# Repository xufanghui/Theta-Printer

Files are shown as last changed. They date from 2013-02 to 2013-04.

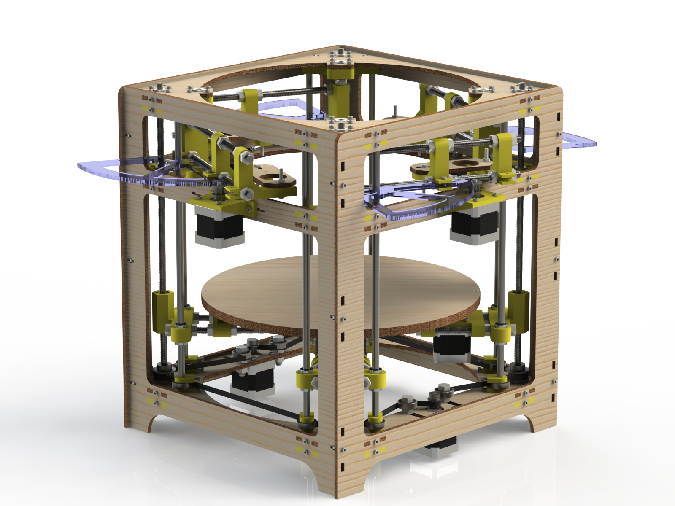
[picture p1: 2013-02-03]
Renders/theta_printer_12.png

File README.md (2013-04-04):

Theta Printer
=============

A polar coordinate based 3D printer with 4 extruders

A magnificent rendering of the Quadricator
[Full Size](http://i.imgur.com/XjrklZc.jpg)

Whats a polar printer?
----------------------
A polar printer works kind of like an old fashioned record player. Your objects are printed onto a platter which spins. The advantage is that you can have many print heads. Each extruder is on the end of an arm which swings in and out. The spinning platter is called the ϴ ("theta") axis and the swinging arm is called the R axis. Together these replace the normal X and Y coordinates you're used to.

Features
--------
+ 4 extruders for multiple colors and materials
+ 320 mm build platter
+ 80425 mm^2 print area (bigger than most repraps)
+ 0.084 degrees/step angular resolution (ϴ Axis)
+ 0.20 mm/step linear resolution (R Axis)
+ Now comes in two versions! The lasercut edition and the reprap edition (printed parts & threaded rods)

ϴ Axis
------
A wooden disk, under which resides a complicated set of motors gears rods and bearings
[Full Size](http://i.imgur.com/GR4uxWu.png)

Objects are printed onto a platter that spins back and forth. Its driven via a stepper motor and a large gear. Rollers support the platter around the perimeter and keep it level.

R Axis
------
Four robotic arms arranged in a diamond shape
[Full Size](http://i.imgur.com/bllIclA.png)

Four Extruders are each mounted on the end of an arm that swings in and out. The blue protractor things are gears for moving the arms.

Z Axis
------
A set of four sprockets with the associated pulleys, motors, and drive belt
[Full Size](http://i.imgur.com/wnbYKVQ.png)

The Z axis is nothing new. Threaded rods in each corner are synchronized by a timing belt and driven by two stepper motors.

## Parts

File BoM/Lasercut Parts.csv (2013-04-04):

ITEM NO. | PART NUMBER | DESCRIPTION | QTY.
1 | Head Holder |  | 8
2 | Arm Rod |  | 8
3 | M8.Nut |  | 149
4 | Arm Center |  | 4
5 | Arm Axis Rod |  | 4
6 | R Gear |  | 4
7 | M3x16.Bolt.91290A120 |  | 172
8 | Extruder Mount Plate |  | 4
9 | M4x30.Bolt.91280A148 |  | 8
10 | M4.Nut.90591A141 |  | 8
11 | Level 1 Corner |  | 8
12 | 608RS Bearing |  | 36
13 | 608 Bearing Cap |  | 1
14 | M3.Nut.90591A121 |  | 172
15 | R Motor Mount |  | 4
16 | Base |  | 7
17 | Cuerpo |  | 7
18 | Tapa |  | 7
19 | B18.6.7M - M3 x 0.5 x 5 Type I Cross Recessed PHMS --5N |  | 28
20 | Eje |  | 7
21 | AFBMA 12.1.4.1 - 0050-11 - 10 | SI | NC | 10_68 | 14
22 | M3x10.Bolt.91290A115 |  | 28
23 | Motor.Sprocket |  | 7
24 | Theta Center |  | 1
25 | M3x30.Bolt.91290A130 |  | 4
26 | Level Z Corner |  | 4
27 | Linear Bearing Body |  | 8
28 | Linear Bearing inside |  | 8
29 | Platter Rod |  | 4
30 | Theta Motor Mount |  | 1
31 | Platter Top |  | 1
32 | Platter Bottom |  | 1
33 | M3x16.Countersunk.Bolt.91294A134 |  | 4
34 | Platter Axle |  | 1
35 | M8.Washer.91455A130 |  | 8
36 | Theta Gear |  | 1
37 | Platter Roller Mount High |  | 1
38 | M8x20.Bolt.91310A533 |  | 3
39 | Platter Roller Mount Low |  | 2
40 | Level 4 Corner |  | 4
41 | Z Smooth Rod |  | 8
42 | Z Rod |  | 4
43 | Z.Rod.Sprocket.a_6z51-036df0610 |  | 4
44 | Smooth Rod Clamp |  | 16
45 | Belt1-1 |  | 1
46 | Level 1 Side |  | 1
47 | Level 2 Side |  | 1
48 | Level 4 Side |  | 1
49 | M8x30.Bolt.91310A536 |  | 4
50 | Side 1 |  | 2
51 | Side 2 |  | 2
52 | 91166A210 |  | 8

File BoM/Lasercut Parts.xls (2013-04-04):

Acquired? | Printed Parts | Description | Qty
1 | Head Holder |  | 8
 | Level 1 Corner |  | 8
✓ | Motor Sprocket |  | 7
✓ | Arm Center |  | 4
 | Level 4 Corner |  | 4
 | Level Z Corner |  | 4
✓ | R Motor Mount |  | 4
✓ | Z Rod Sprocket |  | 4
✓ | Platter Roller Middle |  | 3
 | Theta Center |  | 1
 | Theta Motor Mount |  | 1
 | Laser Cut Parts | Description | Qty | Cost
3 | R Gear | 5mm Acrylic | 4
✓ | Theta Gear | 5mm Acrylic | 1
✓ | Extruder Mount Plate | 5mm Plywood | 4
✓ | Platter Top | 5mm Plywood | 1
✓ | Platter Bottom | 5mm Plywood | 1
✓ | Level 1 Side | 5mm Plywood | 1
✓ | Level 2 Side | 5mm Plywood | 1
✓ | Level 4 Side | 5mm Plywood | 1
✓ | Side 1 | 5mm Plywood | 2
✓ | Side 2 | 5mm Plywood | 2
✓ | 608 Bearing Cap | 5mm Plywood | 1
✓ | Platter Roller Side High |  | 4
✓ | Platter Roller Side Low |  | 2
 | Total |  |  | $60
 | Threaded Rods | Description | Qty | Length (mm) | Total Length | Purchase Qty | Price/Meter | Subtotal
✓ | Arm Rod | M8 1.25 Pitch | 8 | 220 | 1760 | 2000
✓ | Arm Axis Rod | M8 1.25 Pitch | 4 | 110 | 440 | 1000
✓ | Platter Rod | M8 1.25 Pitch | 4 | 400 | 1600 | 2000
✓ | Platter Axle | M8 1.25 Pitch | 1 | 55 | 55 | 1000
✓ | Z Rod | M8 1.25 Pitch | 4 | 430 | 1720 | 2000
✓ | Total |  |  |  | 5575 | 8000 | 4.29 | $34.32 | McMaster | 99055A125 | http://www.mcmaster.com/#catalog/119/3147/=liic32
 | Smooth Rod
✓ | Z Smooth Rod | M8 | 8 | 350 | 2800 | 3200 |  | $49.56 | AliExpress | 707204369 | http://www.aliexpress.com/item/CNC-2pcs-Linear-shaft-400mm-long-diameter-8mm-L-400mm-harden-linear-rod-round-shaft-chrome/707204369.html
 |  |  |  |  |  | 12ft |  | $27.28 | McMaster | 89095K15 | http://www.mcmaster.com/#89095K15
 | Vitamins | Description | Qty | Purchase Qty | Price Each | Subtotal | Supplier | Part # | Link
✓ | 608ZZ Bearing |  | 28 |  |  |  | AliExpress | 609983490 | http://www.aliexpress.com/item/50pcs-lot-608ZZ-608-2RS-8-22-7-Deep-groove-ball-bearing-skate-wheel-bearing/609983490.html
✓ | LM8UU Linear Bearing |  | 8 |  |  |  | AliExpress | 488396282 | http://www.aliexpress.com/item/LM8UU-8mm-Linear-Ball-Bearing-Bush-Bushing-New/488396282.html
✓ | M3.Nut.90591A121 |  | 172 | 200 |  | 2.78 | McMaster | 90591A121 | http://www.mcmaster.com/#catalog/119/3167/=l4j9dm
✓ | M3x10.Bolt.91290A115 |  | 28 | 100 |  | 5.02 | McMaster | 91290A115 | http://www.mcmaster.com/#catalog/119/3093/=l4j9n6
✓ | M3x16.Bolt.91290A120 |  | 176 | 200 |  | 12.1 | McMaster | 91290A120 | http://www.mcmaster.com/#catalog/119/3093/=l4j9rl
✓ | M3x16.Countersunk.Bolt.91294A134 |  | 4 | 100 |  | 11.67 | McMaster | 91294A134 | http://www.mcmaster.com/#catalog/119/3102/=l4ja5r
✓ | M3x30.Bolt.91290A130 |  | 4 | 0 |  | 0 | McMaster | 91290A130 | http://www.mcmaster.com/#catalog/119/3093/=l4jb78
✓ | M4.Nut.90591A141 |  | 8 | 100 |  | 1.39 | McMaster | 90591A141 | http://www.mcmaster.com/#catalog/119/3167/=l4jbpz
✓ | M4x30.Bolt.91280A148 |  | 8 | 100 |  | 7.96 | McMaster | 91280A148 | http://www.mcmaster.com/#catalog/119/3129/=l4jcc0
✓ | M8.Nut | 1.25mm Pitch | 149 | 200 |  | 9.02 | McMaster | 90592A022 | http://www.mcmaster.com/#hex-nuts/=l4je22
✓ | M8.Washer.91455A130 |  | 8 | 100 |  | 6.09 | McMaster | 91455A130 | http://www.mcmaster.com/#catalog/119/3202/=l4jej3
✓ | M8x20.Bolt.91310A533 |  | 3 | 0 |  | 0 | McMaster | 91310A533 | http://www.mcmaster.com/#catalog/119/3128/=l4jf1j
✓ | M8x30.Bolt.91310A536 |  | 4 | 25 |  | 7.91 | McMaster | 91310A536 | http://www.mcmaster.com/#standard-cap-screws/=ld4026
 | Motor.Sprocket | 18 Grooves | 7 | 0 | 5.81 | 0 | SDP/SI | A 6T16M018DF6005 | https://sdp-si.com/eStore/PartDetail.asp?Opener=Group&PartID=42977&GroupID=347
4 | NEMA 17 |  | 7
✓ | Z Belt | GT2 1210.00 mm | 1 | 1 | 9.32 | 9.32 | SDP/SI | A 6R51M605060 | https://sdp-si.com/eStore/PartDetail.asp?Opener=Order&PartID=75945&GroupID=342&Qty=0
✓ | Z Belt | GT2 1228.00 mm | 1 | 1 | 9.32 | 9.32 | SDP/SI | A 6R51M614060 | https://sdp-si.com/eStore/PartDetail.asp?Opener=Order&PartID=75946&GroupID=342&Qty=0
 | Z.Rod.Sprocket |  | 4 | 0 | 6.18 | 0 | SDP/SI | A 6Z51-036DF0610 | https://sdp-si.com/eStore/PartDetail.asp?Opener=Group&PartID=55833&GroupID=218
 | Total |  |  |  |  | $82.58
 | Total Cost | $226.46

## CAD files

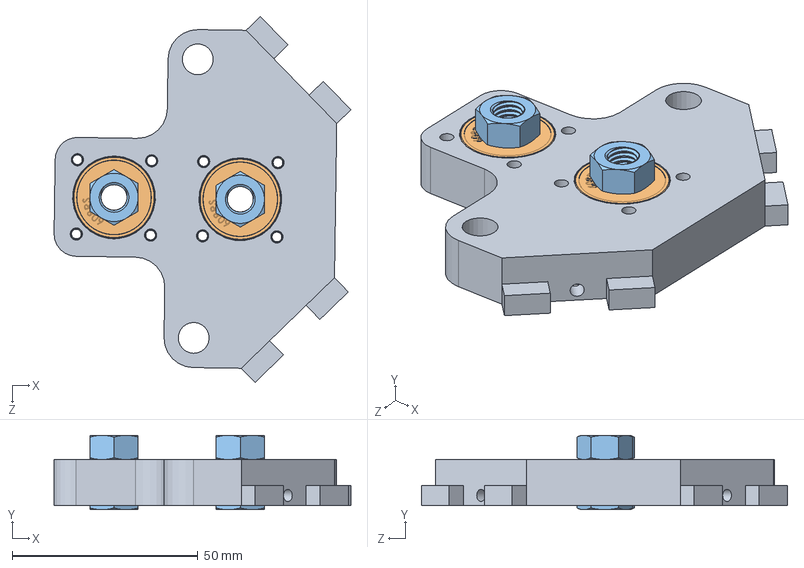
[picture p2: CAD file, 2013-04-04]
Level 1 Corner Assembly.SLDASM
79.9 x 20.0 x 98.5 mm
Level 1 Corner
608RS Bearing x 2
M8.Nut x 4
M3.Nut.90591A121 x 8

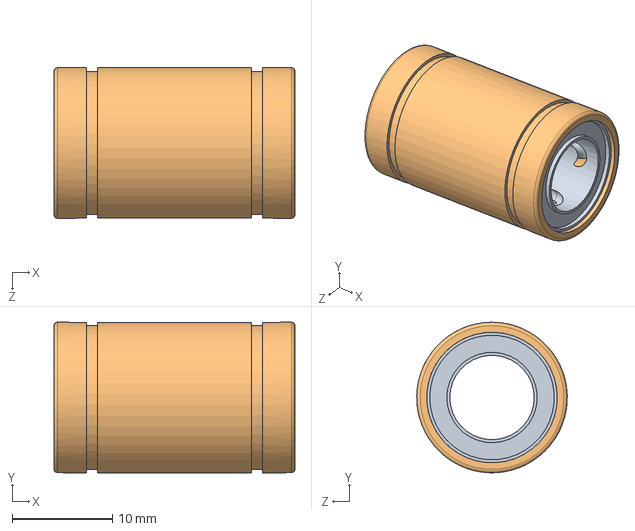
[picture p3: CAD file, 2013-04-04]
Vitamins/LM8UU/Linear Bearing animation.SLDASM
24.0 x 15.0 x 15.0 mm
Linear Bearing Body
Linear Bearing inside

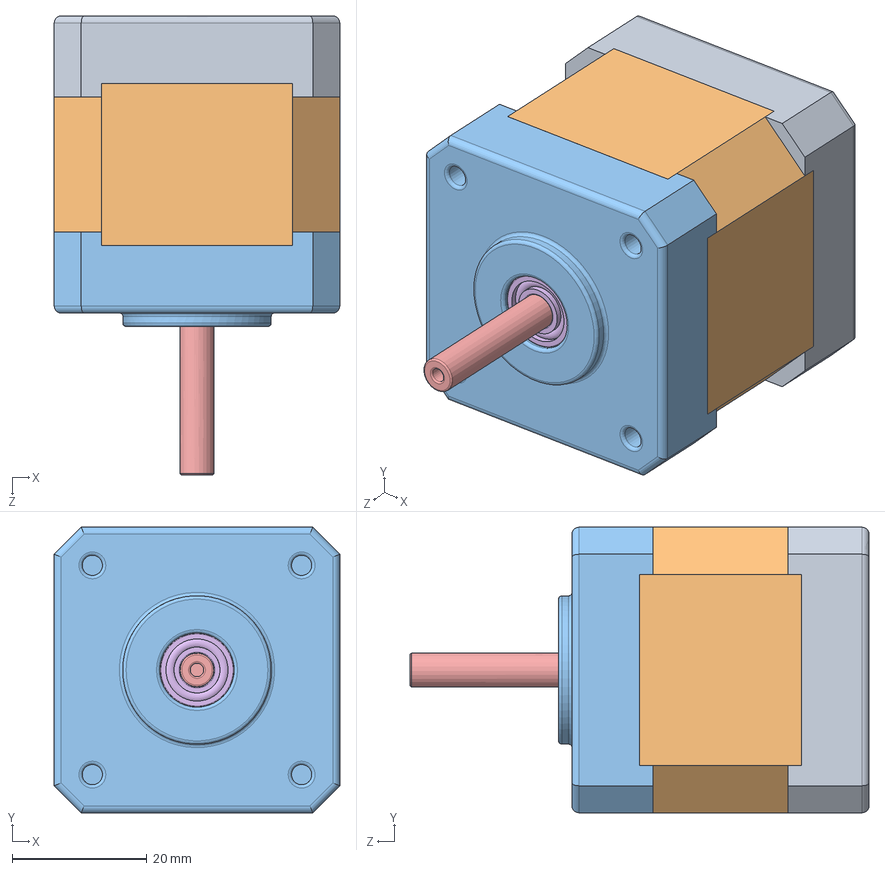
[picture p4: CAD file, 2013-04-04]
Vitamins/NEMA 17/NEMA 17.SLDASM
42.3 x 42.3 x 68.0 mm
Base
Cuerpo
Tapa
pan cross head_am x 4
Eje
instrument ball bearing_68_am x 2

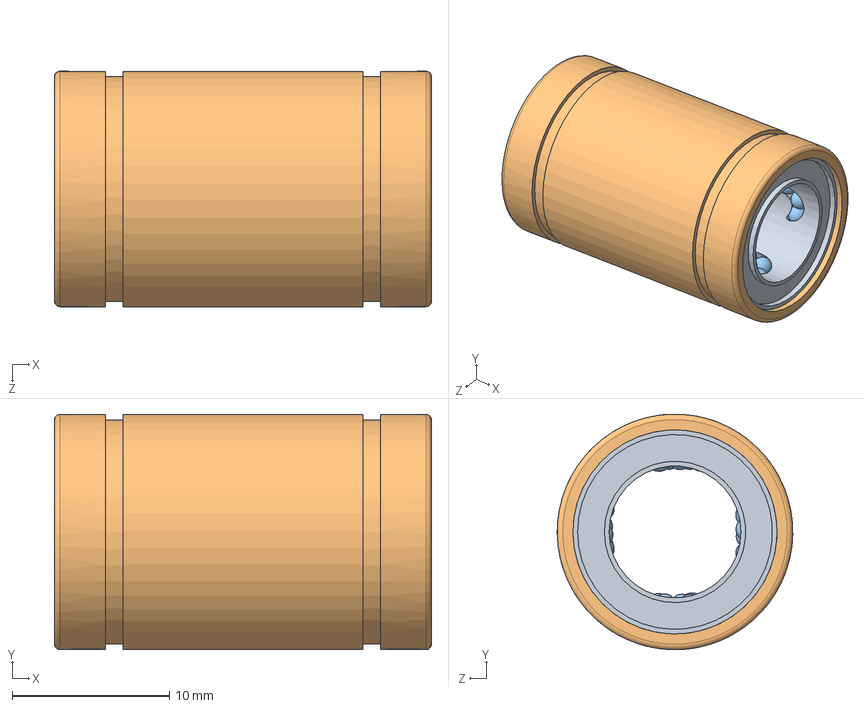
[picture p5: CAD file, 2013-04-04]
Vitamins/LM8UU/LU8MM.SLDASM
24.0 x 15.0 x 15.0 mm
Linear Bearing Body
Linear Bearing inside
Municion x 102

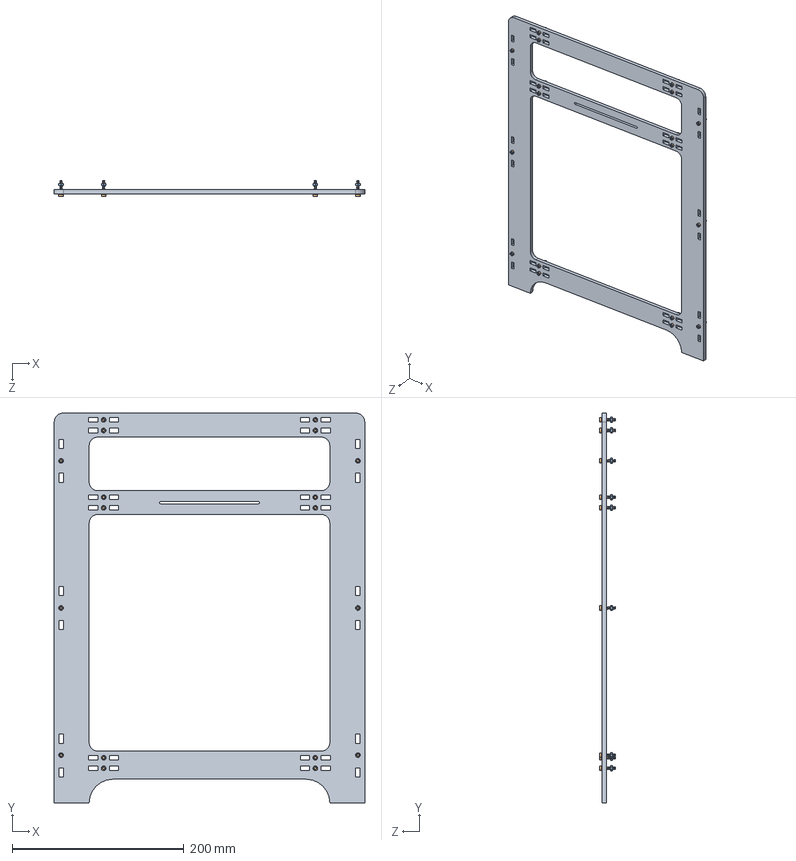
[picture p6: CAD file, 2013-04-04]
Side 2 Assembly.SLDASM
361.3 x 453.7 x 19.0 mm
Side 2
M3x16.Bolt.91290A120 x 18
M3.Nut.90591A121 x 18

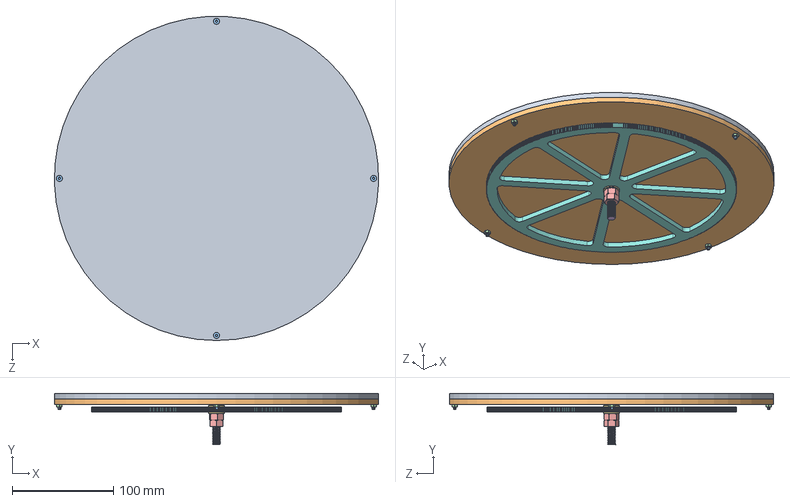
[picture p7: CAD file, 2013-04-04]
Platter Assembly.SLDASM
319.9 x 50.6 x 319.7 mm
Platter Top
Platter Bottom
M3x16.Countersunk.Bolt.91294A134 x 4
M3.Nut.90591A121 x 4
M8.Nut x 3
Platter Axle
M8.Washer.91455A130 x 2
Theta Gear

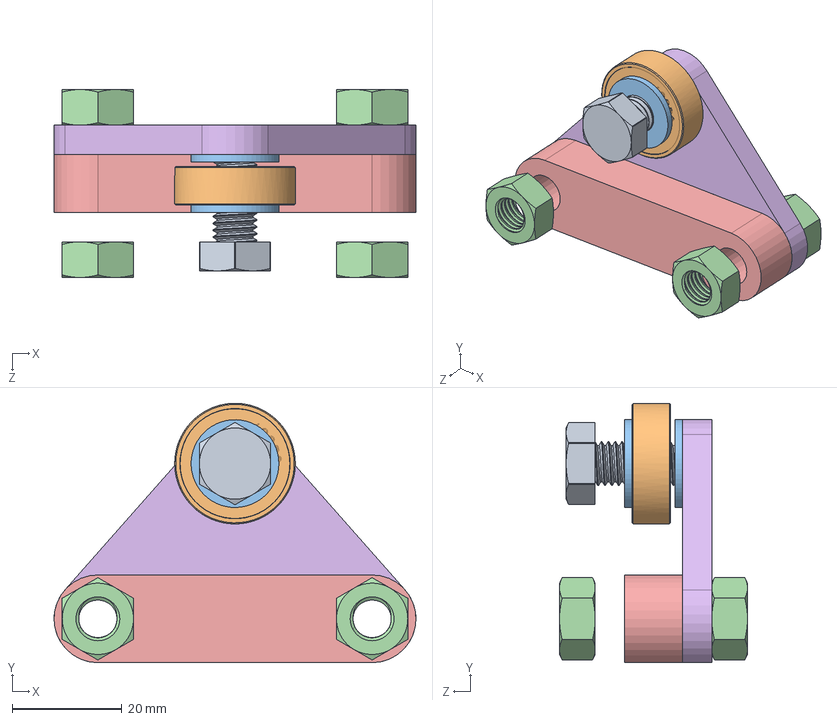
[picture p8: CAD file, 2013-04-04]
Platter Roller Assembly.SLDASM
66.0 x 47.3 x 34.3 mm
M8x20.Bolt.91310A533
608RS Bearing
M8.Washer.91455A130 x 2
M8.Nut x 4
Platter Roller Middle
Platter Roller Side

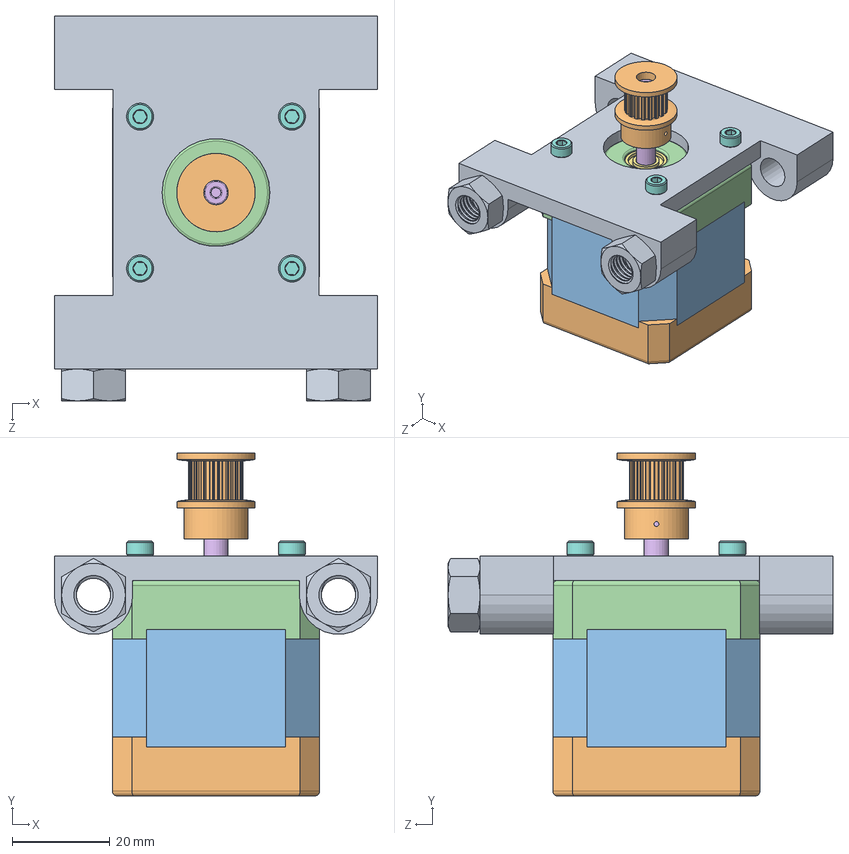
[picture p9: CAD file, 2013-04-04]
Theta Motor Assembly.SLDASM
66.0 x 70.0 x 78.5 mm
Theta Motor Mount
Base
Cuerpo
Tapa
pan cross head_am x 4
Eje
instrument ball bearing_68_am x 2
M3x10.Bolt.91290A115 x 4
M8.Nut x 2
Motor.Sprocket

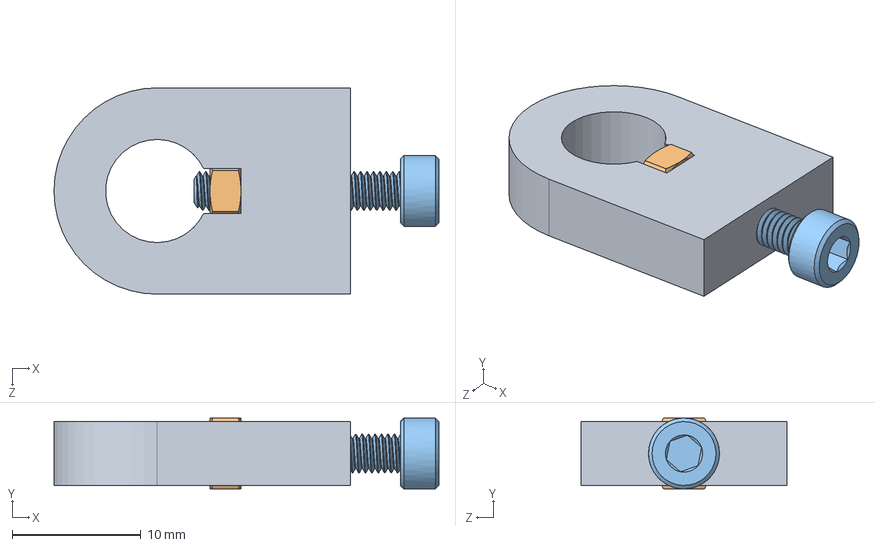
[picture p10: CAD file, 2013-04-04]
Smooth Rod Clamp Assembly.SLDASM
29.9 x 5.50 x 16.0 mm
Smooth Rod Clamp
M3.Nut.90591A121
M3x16.Bolt.91290A120

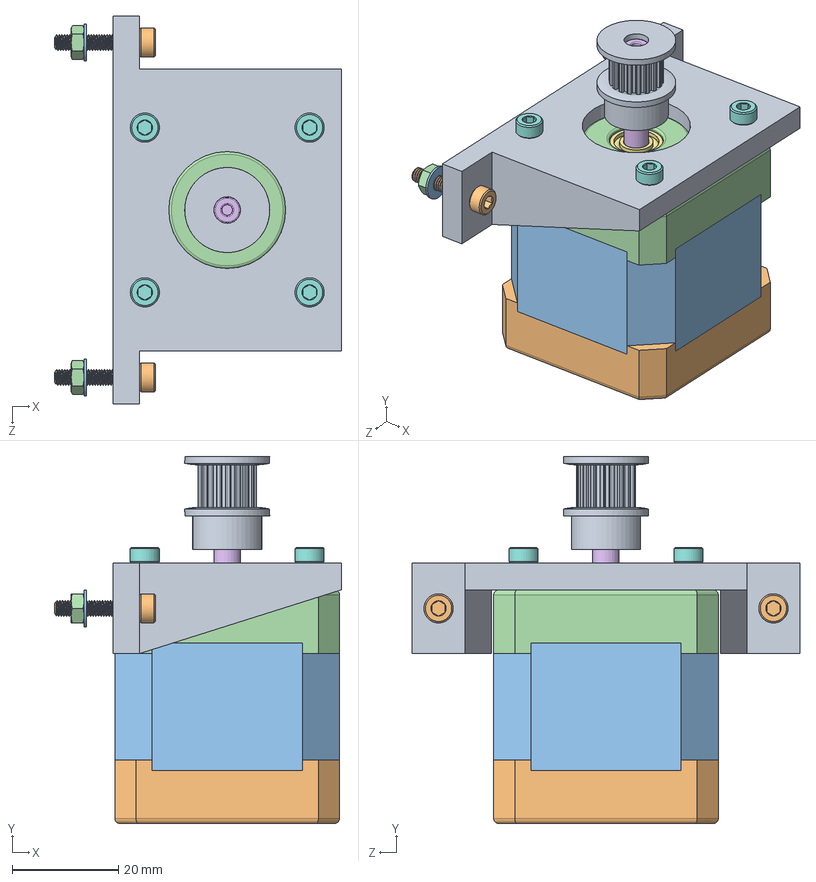
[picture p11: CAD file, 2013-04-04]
R Motor Assembly.SLDASM
54.0 x 69.1 x 73.0 mm
R Motor Mount
Base
Cuerpo
Tapa
pan cross head_am x 4
Eje
instrument ball bearing_68_am x 2
M3x10.Bolt.91290A115 x 4
Motor.Sprocket
M3x16.Bolt.91290A120 x 2
M3.Washer.91166A210 x 2
M3.Nut.90591A121 x 2

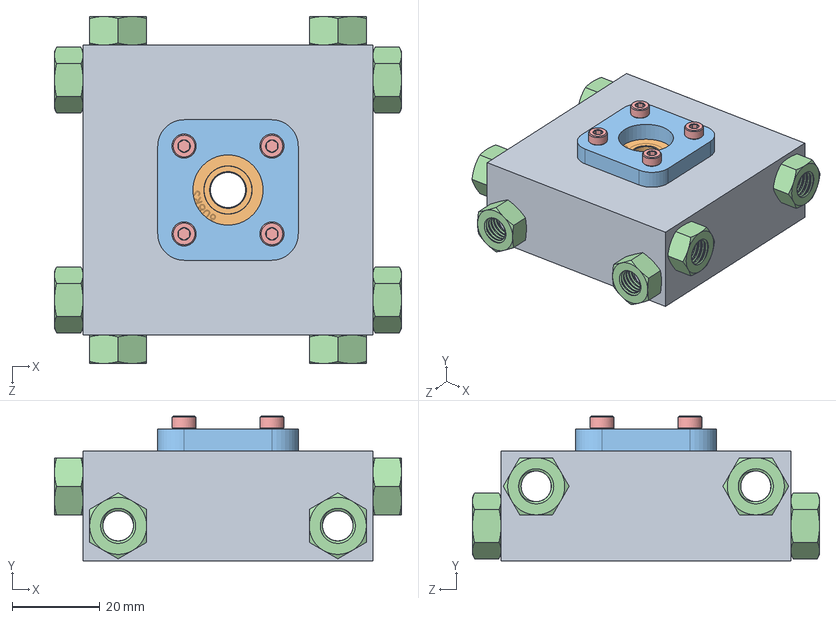
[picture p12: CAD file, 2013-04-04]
Theta Center Assembly.SLDASM
79.0 x 33.0 x 79.0 mm
Theta Center
608RS Bearing
608 Bearing Cap
M8.Nut x 8
M3x16.Bolt.91290A120 x 4
M3.Nut.90591A121 x 4

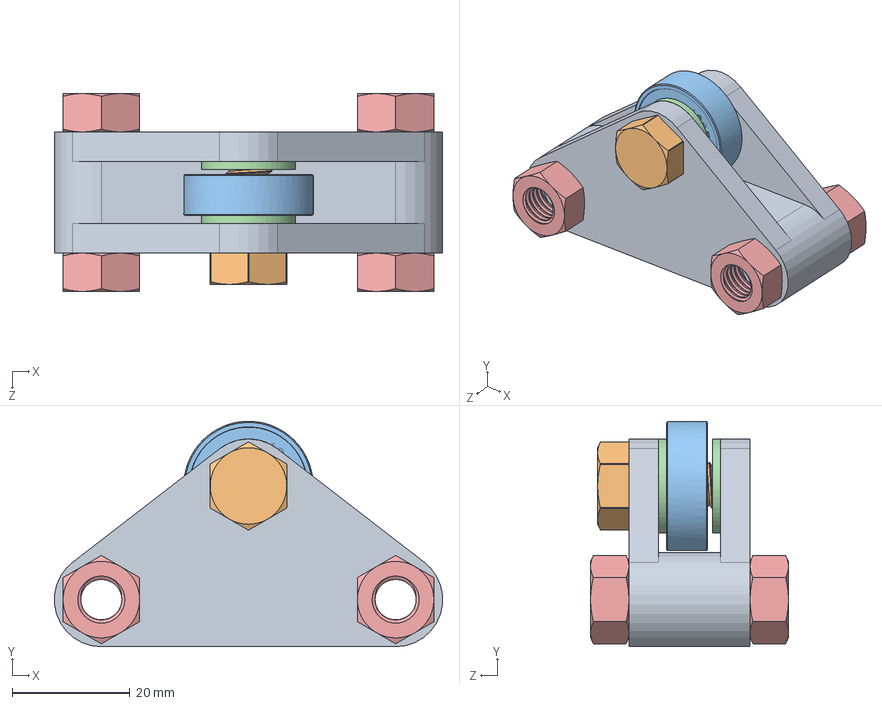
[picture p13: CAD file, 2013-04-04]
Platter Roller Assembly High.SLDASM
65.9 x 38.3 x 33.6 mm
Platter Roller Mount High
M8x20.Bolt.91310A533
608RS Bearing
M8.Washer.91455A130 x 2
M8.Nut x 4

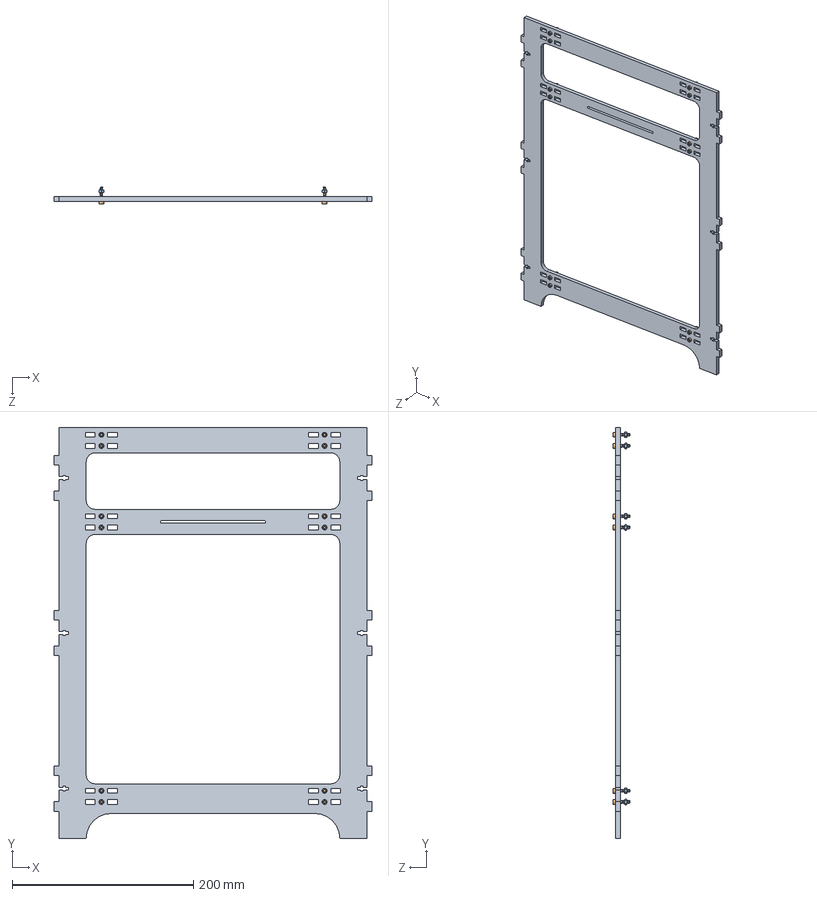
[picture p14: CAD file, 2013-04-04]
Side 1 Assembly.SLDASM
350.7 x 453.7 x 19.0 mm
Side 1
M3x16.Bolt.91290A120 x 12
M3.Nut.90591A121 x 12

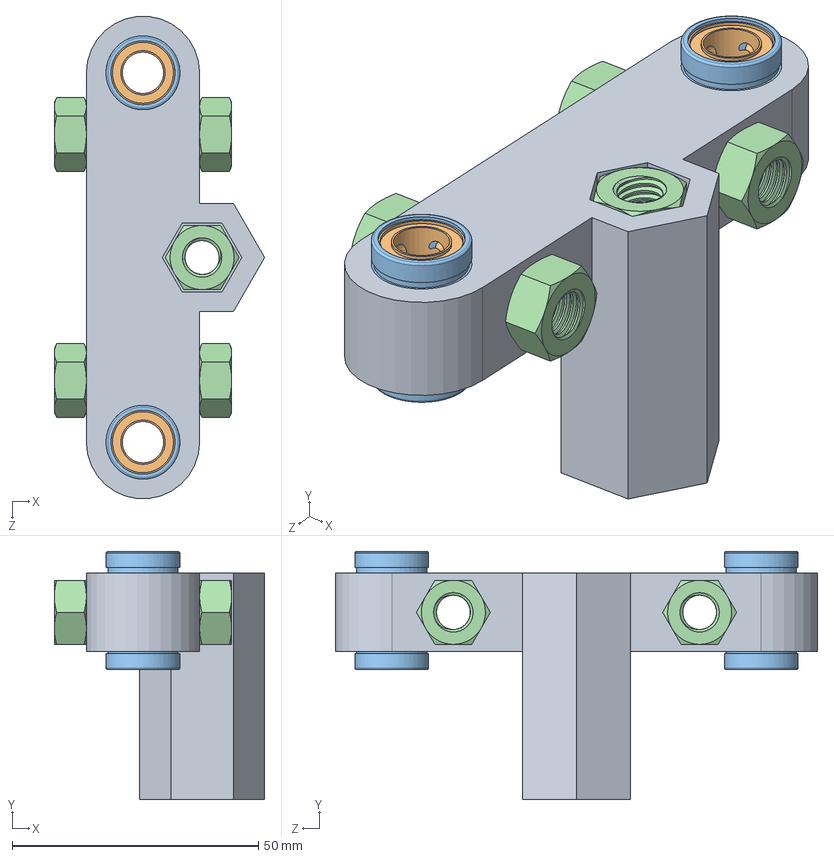
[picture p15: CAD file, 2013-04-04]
Level Z Corner Assembly.SLDASM
42.7 x 50.3 x 97.9 mm
Level Z Corner
Linear Bearing Body x 2
Linear Bearing inside x 2
M8.Nut x 5

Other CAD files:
Vitamins/LM8UU/LM8UU.SLDASM
Platter Roller Assembly Low.SLDASM
DXFs/Platter Roller Side.High.DXF
Rods/Platter Axle.SLDPRT
608 Bearing Cap.SLDPRT
Arm Center.SLDPRT
Belt1-1.sldprt
BoM/Bill of Materials.SLDDRW
Bottom Sketch.SLDPRT
DXFs/608 Bearing Cap.DXF
DXFs/Extruder Mount Plate.DXF
DXFs/Level 1 Side.DXF
DXFs/Level 2 Side.DXF
DXFs/Level 4 Side.DXF
DXFs/Platter Bottom.DXF
DXFs/Platter Roller Side.Low.DXF
DXFs/Platter Top.DXF
DXFs/R Gear.DXF
DXFs/Side 1.DXF
DXFs/Side 2.DXF
DXFs/Theta Gear.DXF
Extruder Mount Plate.SLDPRT
Head Holder.SLDPRT
Level 1 Corner.SLDPRT
Level 1 Side.SLDPRT
Level 2 Side.SLDPRT
Level 4 Corner.SLDPRT
Level 4 Side.SLDPRT
Level Z Corner.SLDPRT
Platter Bottom.SLDPRT
Platter Roller Middle.SLDPRT
Platter Roller Mount High.SLDPRT
Platter Roller Mount Low.SLDPRT
Platter Roller Side.SLDPRT
Platter Top.SLDPRT
R Gear.SLDPRT
R Motor Mount.SLDPRT
Rods/Arm Axis Rod.SLDPRT
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

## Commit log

2013-02-03 New Lasercut Edition
    [Arm Axis Rod.SLDPRT, Arm Center.SLDPRT, Arm Rod.SLDPRT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]
2013-04-04 Generated STLs & DXFs, and numerous improvements.
    [608 Bearing Cap.DXF, 608 Bearing Cap.SLDPRT, 608RS Bearing.SLDPRT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]
2013-04-04 Remove old junk.
    [Level 2 Corner.SLDPRT, R Axis Corner Assembly.SLDASM, R Axis Corners.SLDPRT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]
